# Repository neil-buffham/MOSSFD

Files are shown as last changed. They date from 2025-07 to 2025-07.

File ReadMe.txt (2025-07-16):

# Modular Open Source Split-Flap Display
(MOSSFD)
--------------------------------------------------------------------------------------------------------------------------------
This project is a Mechanical "Split-Flap" display based on:
- ESP32-WROOM-32D microcontroller
- 28BYJ-48 5V DC Stepper Motor
- ULN2003AN BWQ 2436C motor driver
- A3144 digital hall effect sensor

The display is designed to be built with identical modules based on these components. The modules can be connected in chain to form a display. For now, individual power is supplied to each unit, but on small scales, power can be daisy-chained instead. The modules I built use a JST 5 pin connector to connect RX, TX, "Detect", GND, and 5v, but you could use whatever 5 pin you felt like. (If you use VGA connectors please send me a picture). The hardware in the array is identical, but one module operates as the "Master", which is currently able to:
- Receive input from Serial Com (For example the Arduino IDE or other program)
- Scan this "Paragraph_message" for its own unique (mac-based) ID and perform the assigned command
- Forward this message to the other modules.

The other modules in the array scan the paragraph_message for their ID, and perform the command connected to their ID.

Current commands include (with a few notes about upcoming changes)
any letter    - Check if the character is in their index/drum, then move to that character.
***INFO       - Print current information                    //update
***ZERO       - Re-index using magnet			     //Possibly add slow zero
***<number>   - Move to flap index by number                 //Verify working after combined logic
***POS        - Print current step and degree position       //Possibly integrate to info / delete
***LIST       - Print character index list                   //.
***RESET      - Restart the ESP32                            //.
***REV        - Measure steps in one revolution              //Probably delete
***COUNT      - Show magnet pass count                       //Integrate/delete
***MOVE <N>   - Move forward by N steps                      //Delete
***ZOFFSET    - Set magnet-to-flap offset in degrees         //Cleanup + clean debug
***OFFSET     - Set global step offset                       //Cleanup + clean debug
***RESETCONFIG - Reset stored config to default values       //.
***HELP       - Show this help message                       //Update to match
***LEFTMODE   - Enable left-module input mode                //Update to match new logic
****[message] - Inject paragraph_message (for dev testing)   //Note: only available in MasterMode

At present the master module is kind of buggy, and needs some notable firmware work. It is not capable yet of creating the "paragraph_message", but will hopefully be able to do so soon. For now, I've been using a python script to parse text into a use-able paragraph message, which is then sent via Serial comm (Baud 11520 for PC -> Module communication) to the master module.

The paragraph_message is composed as follows:
**** //denotes that the following is a paragraph_message
[] //the beginning/end of the contents of the paragraph_message
{} //encompasses the master ID, which is sent at the beginning of each paragraph_message. This will be utilized later in development
| //divides the message from the master into chunks that are applicable to each unit
: //divides the portion of the message that is applicable to each unit into sections

Example: 9 module display, showing:
012345678

****[{14146C1C4278}|14146C1C4278:0:0|E0F76B1C4278:1:0|0445470B65F4:2:0|F893963B015C:3:0|2C1A6D1C4278:4:0|9CDC550B65F4:5:0|5CB469BF1388:6:0|1CF861BF1388:7:0|848A6C1C4278:8:0]

For the same command being sent to all modules, FFFF can be used. Ex:
- FFFF Character Commands //Set all modules to the same character, in this example a tilde.
 	****[{FFFF}|FFFF:~:0]
- FFFF Zero Commands //"Zero" all modules, re-indexing the start position using the hall effect sensor and the magnet
 	****[{FFFF}|FFFF:***ZERO:0]
- FFFF Reset Commands //Roughly equivalent to hitting the reset button. Makes the modules perform the startup sequence, which includes zero-ing.
 	****[{FFFF}|FFFF:***RESET:0]

//note: several of these functions are probably broken as of 7/15/2025
--------------------------------------------------------------------------------------------------------------------------------
I drew a custom PCB to be optionally used to house the Arduino and motor driver and provide more streamlined assembly (Just screw in your cables, assemble the 3d printed parts, and hot glue in the Hall effect, if you are into that kind of thing. It is NOT required, and I attempted to document the parts well in the spreadsheet. (There is a BOM as well.) If you choose to use the PCB, you will need to either solder jumper wires or get a bunch of jumping pins, as the "custom" non-esp32-standard-breakout parts are almost all in the bottom half and electrically isolated in case you change your mind and just want to use it as an ESP32 breakout. For reference, I was able to order 10 PCBA (assembled) units for $20 a pop (I don't like to think about it, questionably wise), and 20 non-assembled units for a "total" of $38.34 + $28 in import fees, which equates to ~$66.34 total or $3.34 per un-assembled part-less board. The Google sheets has a much better breakdown. Essentially, if you want to pay $15 per module for electronics and $5-$8 in printing costs, don't get a PCBa order. If you want to pay $40 for electronics and also $5-$8 for printing costs but reduce the assembly to screwing down 13 to 23 labeled cables (for left com, right com, Hall effect, and then possibly top / bottom comm {which are not supported in firmware yet}) and plugging in the motor cable, get the PCBA. If you want to pay about $18 per module for electronics and have a lot of soldering to do on top of the above cable-screwing, but prefer "solder in these headers" to "Attach D34 to the hall effect sensor OUT pin, which needs to have a 10k Resistor wired to the 3.3v pin...", then get a non-assembled PCB and order the parts. If you want to figure out import/duty fees, order the pcb components for assembly from China. Otherwise, Amazon has most of the parts, and if you find the right angle SMD xt30 you are a wizard.
--------------------------------------------------------------------------------------------------------------------------------
## License

This project uses a dual license approach:

- **Code (firmware, Arduino libraries)**: [GNU GPL v3.0](./LICENSE)
- **Design files (STLs, skp, skb, 3mf, fusion, onshape, other CAD, schematics, images, etc.)**: [Creative Commons BY-SA 4.0](./LICENSE.design)

Unless otherwise noted, source code files fall under GPLv3, and non-code files under CC BY-SA.
--------------------------------------------------------------------------------------------------------------------------------
### Disclaimer of Patent Liability

These files are provided under open licenses (GPL and CC BY-SA), but no patent rights are granted or implied.  
If use of this project or any of its parts infringes on third-party patents, you use it at your own risk.  
The author makes no warranties regarding patent freedom.
--------------------------------------------------------------------------------------------------------------------------------
### Disclaimer of Warranty

This project is provided "as is", without warranty of any kind — express or implied — including but not limited to the warranties of merchantability, fitness for a particular purpose, and noninfringement.  
In no event shall the author be liable for any claim, damages, or other liability arising from the use of this project, whether in an action of contract, tort, or otherwise.  
Use it at your own risk.
--------------------------------------------------------------------------------------------------------------------------------
In respect to the license, essentially you can:

- [✓] Use this project for personal or commercial purposes  
- [✓] Modify the code and designs  
- [✓] Share or remix your modified versions  
- [✓] Sell hardware or software based on it  

As long as you:

- [*] **Share improvements** under the same licenses (GPL for code, CC BY-SA for designs)  
- [*] **Give credit** to the original author (Neil Buffham)  
- [*] **Include the original license texts** when redistributing  
- [ ] **Do not** apply DRM or restrict others from doing these same things 

See the full license texts for legal details:  
- `LICENSE` for code (GPL v3)  
- `LICENSE.design` for designs (CC BY-SA 4.0)

Note: This is a human-friendly summary. The full license texts are authoritative and take precedence.
--------------------------------------------------------------------------------------------------------------------------------
Used in this project:

Overpass Mono Font  
- Source: https://fonts.google.com/specimen/Overpass+Mono  
- License: SIL Open Font License 1.1 (OFL) — https://openfontlicense.org  
- Copyright: © 2024 Red Hat, Inc.  
- Permission is granted to use, modify, and redistribute the font under the terms of the OFL.  
- The font is used in a slightly modified form for the characters on the flaps

AccelStepper Library  
- Source: https://docs.arduino.cc/libraries/accelstepper/  
- GitHub: https://github.com/waspinator/AccelStepper  
- License: GNU GPL v3.0 — https://www.gnu.org/licenses/gpl-3.0.html  
- Author: Mike McCauley / AirSpayce  
- The AccelStepper library is used in firmware to control the stepper motor.

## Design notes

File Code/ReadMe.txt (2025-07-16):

/*See Readme file. V005 attempts to overcome rounding float issues that
were resulting in the displayed index being off by 1 in V004.

V2005 includes:
- Better help menu
- (new) Info command
- added manually assigned steps for each flap in flap_index.h
- added a value and a function to apply adjustments to this value
- cleaned print functions to have divider lines between

Iterated to v2006 because it works now, and some features in v2006 may
interrupt active process' and change the logical flow of the offset-setting
commands. Thanks for reading.
*/

/*You will likely need to download a windows driver depending on your
ESP32 Board of choice. You will also need to add the ESP32 boards to
your arduinno IDE. Below is an example board and driver needed:

https://a.co/d/9pYIOlR
https://www.silabs.com/developer-tools/usb-to-uart-bridge-vcp-drivers?tab=downloads
for this board, the "Universal Windows Driver" works. Go to device manager and find
the device, then select the downloaded/extracted driver for "update driver" 

For me it showed up under the "Other Devices" as CP2102 USB to UART Bridge Controller
If you select the folder one level above x64 / x86 etc. it finds the correct driver.

In the Arduino IDE, I selected the ESP32 Dev Module as the board.
*/

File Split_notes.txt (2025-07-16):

Next firmware goals:
- Move back to a single-logical parsing situation by having a variable ActiveListenSerial, this way hopefully
   we can define multiple serial connections, but do our parsing based on what serial is listened to at present.
- With that, possibly combine back into one firmware instead of a forked Master/Slave pair
- Potentially provision for a button or switch or jumper to change between LEFTMODE and MASTERMODE
- Clean up the info and Zoffset data/debug information
- Add a motor power off timeout function
- Add a permanent variable that serves like an odometer, just because it would be interesting and we are already tracking rotations.
- Update available commands:

---
Available Commands:
***INFO       - Print current information                    //update
***ZERO       - Re-index using magnet			     //Possibly add slow zero
***<number>   - Move to flap index by number                 //Verify working after combined logic
***POS        - Print current step and degree position       //Possibly integrate to info / delete
***LIST       - Print character index list                   //.
***RESET      - Restart the ESP32                            //.
***REV        - Measure steps in one revolution              //Probably delete
***COUNT      - Show magnet pass count                       //Integrate/delete
***MOVE <N>   - Move forward by N steps                      //Delete
***ZOFFSET    - Set magnet-to-flap offset in degrees         //Cleanup + clean debug
***OFFSET     - Set global step offset                       //Cleanup + clean debug
***RESETCONFIG - Reset stored config to default values       //.
***HELP       - Show this help message                       //Update to match
***LEFTMODE   - Enable left-module input mode                //Update to match new logic
****[message] - Inject paragraph_message (for dev testing)   //Note: only available in MasterMode

Type any single character to move to that flap.              //Eh, probably fine

---

Current array:
14146C1C4278
E0F76B1C4278
0445470B65F4
F893963B015C
2C1A6D1C4278
9CDC550B65F4
5CB469BF1388
1CF861BF1388
848A6C1C4278

D4836C1C4278 //known issues

****[{14146C1C4278}|14146C1C4278:0:0|E0F76B1C4278:1:0|0445470B65F4:2:0|F893963B015C:3:0|2C1A6D1C4278:4:0|9CDC550B65F4:5:0|5CB469BF1388:6:0|1CF861BF1388:7:0|848A6C1C4278:8:0]

****[{14146C1C4278}|D4836C1C4278:***reset:0]

---
Current Firmwares: V2009-2_Master, V2009-3_Slave
Working:
- Space character
- FFFF Character Commands
 	****[{FFFF}|FFFF:~:0]
- FFFF Zero Commands
 	****[{FFFF}|FFFF:***ZERO:0]
- FFFF Reset Commands
 	****[{FFFF}|FFFF:***RESET:0]

NOT WORKING:
- the characters - on only the master firmware. Slave works fine.
 	Scratch that. It was finnicky but went eventually.
 	- / ,

- Master module individual commands finnicky
 	- Help works
 	- Reset and Zero do not
 	- Seems like the rest of the commands don't work (They are split into a separate portion in code)

***Zoffset0 - Displayed "," when commanded character "%"
***Zoffset72 - Displayed "@" when commanded character "%"
***Zoffset144 - Displayed '"' when commanded character "%"
***Zoffset216 - Displayed '!' when commanded character "%"
***Zoffset4032 - Displayed '/' when commanded character "%"
***Zoffset353 - Displayed '&' when commanded character "%"

***Zoffset90 - Displayed '@' when commanded character "%"

/*
  Zero Offset Reference Table (evenly spaced around 91.00°)

  Use with ***ZOFFSET<degrees> command
  Each row represents a full-degree step
  One flap ≈ 6.32°

// Steps   Degrees     Flap Offset (approx)
// ------  --------     ---------------------
//   927     81.47°         -1.50 flaps
//   939     82.50°         -1.35 flaps
//   951     83.53°         -1.20 flaps
//   963     84.56°         -1.04 flaps
//   975     85.59°         -0.90 flaps
//   987     86.62°         -0.75 flaps
//   999     87.66°         -0.60 flaps
//  1011     88.69°         -0.45 flaps
//  1023     89.72°         -0.30 flaps - two modules are currently set to this
//  1035     90.75°         baseline (ideal)
//  1047     91.78°         +0.15 flaps
//  1059     92.81°         +0.30 flaps
//  1071     93.84°         +0.45 flaps
//  1083     94.88°         +0.60 flaps
//  1095     95.91°         +0.75 flaps
//  1107     96.94°         +0.90 flaps
//  1119     97.97°         +1.04 flaps
//  1131     99.00°         +1.20 flaps
//  1143    100.03°         +1.35 flaps
//  1155    101.06°         +1.50 flaps

*/

---

2 - Motor_offset
3 - Bottom
3 - Drum_57
3 - Drum_57_lid
4 - Right_Wall
7 - Left_wall
7 - Lid_(wide)
8 - Motor_Bracket
2 - PCB_tray
2-5 - Flaps (Special Characters)

Microcontroller:
ESP32-WROOM-32D

28BYJ-48 5V DC Stepper Motor with
ULN2003AN BWQ 2436C motor driver chip in a breakout board

A3144 hall effect sensor (3 pin) - note that the side with the writing is the front face, and needs to interact with a magnet's South pole.
  Pin 1 (left)   -   VCC (typically 5V)
  Pin 2 (middle) -   GND
  Pin 3 (right)  -   OUT (signal to ESP32, use 10kohm pullup resistor wired to 3.3v)
    one wire straight from the pin to the esp32
    one wire from the esp32 through the 10kohm resistor to the 3.3v pin.

Connectors for module to module communication:
  1 - VCC (Shared 5v Power)
  2 - GND (Shared ground)
  3 - RX (incoming data)
  4 - TX (outgoing data)
  5 - Presence/detect (sense neighboring modules/ESP's) //likely not used in current-version code

Buttons:  //these are not populated in current version hardware.
  BTN1 - GPIO36 (VP) - Use internal Pullup resistor and wire opposite to GND
  BTN2 - GPIO39 (VN) - Use internal Pullup resistor and wire opposite to GND

Wiring notes:
5V and GND bus bars:
10 screw bus bar for Ground
  4 for the top/bottom/side/side communication
  2 for the buttons
  1 for the type c 5VIN ground connector
  1 for the ESP32 ground connector
  1 for the Hall Effect Sensor
  1 for the Motor Driver

8 screw bus bar for 5V
  4 for the top/bottom/side/side communication
  1 for the type c 5VIN connector
  1 for the ESP32 VIN
  1 for the Hall Effect Sensor
  1 for the Motor Driver

---
Goal for now: Get a "Send-only" network together where there are only two code types: The Master unit, and Slave units.
The master parses a "serial monitor" input from the Arduino IDE, and spits out a paragraph style text over a module-to-module
serial connection (RX and TX). Each slave unit knows its own identifier, but nothing else in relation to the display. They
don't "dabble" in anything besides searching the serial-received message for the chunk that contains their identifier, forwarding
the serial message on to the right, and following the command that they received. The only other thing that each module needs to
"be aware" of is FFFF. They should be set up to look for FFFF in the paragraph message that is sent in the same way they look for
their own ID, and follow commands stated to FFFF. There might need to be own ID vs FFFF logic later, but not yet.

While perhaps not the most logical, for now I want each module, including the master, to both store and process the paragraph
message. This will hopefully avoid too many branches of active code that need to function together (ex. master code execution vs.
slave code execution + timing + "finished" handling, etc.

I think a logical way to do this will be to have Some pre-determined dividers:
[] //means the beginning/end of the message that is sent from the master
{} //encompass the master ID
| //divide the message from the master into chunks that are applicable to each unit
: divide the portion of the message that is applicable to each unit into sections

The sections:
[{MasterID}|SlaveID:Character or code:Status|SlaveID:Character or code:Status

Third value: status
0 = no modifier //go to character or perform code immediately. Eventually blank might call this function as well.
1 = no command detected yet
7 = parse_error //could not parse a useable command out of the paragraph_message
8 = execution_error //the command was not completed
9 = complete //the last command was completed correctly - used for internal recording, not communication yet.

/*
//- Soon we may try to implement "hold"/wait functionality, but not yet.
 = Hold //Store value but don't go yet
 =  Go //Go to stored value, or "" if no value present //There should always be a value present
*/

/*
//- The following are in ideation only and should be nearly entirely ignored. Do not cater to them.
 = Finished //From the master module's perspective, this is not a "TX" value, this would be recieved.
 = Received //Character received
*/

Example setup:
Master: 14146C1C4278
Slave1: 0445470B65F4
Slave2: 848A6C1C4278

Example outputs:
ABC
No delays or holds, just go now:
[{14146C1C4278}|14146C1C4278:A:0|0445470B65F4:B:0|848A6C1C4278:C:0]

DOG
No delays or holds, just go now:
[{14146C1C4278}|14146C1C4278:A:0|0445470B65F4:B:0|848A6C1C4278:C:0]

Reset all modules now:
[{14146C1C4278}|FFFF:***Reset:0]

Zero all modules now:
****[{FFFF}|FFFF:***ZERO:0]

---

With this in mind, I think that each module will need local processing for the following:
- Serial receive(Left)
- Serial write(Right)

- A variable for it's own ID (already implemented)
- A "Status" variable that notes if the module is ready to receive the p. message
- long text variable to store the paragraph

current_command - A variable to store the command or character decided by the paragraph message
current_command_status - A variable to store the status declared by the paragraph message

- Several Boolean variables:
  - One to record that a new paragraph message has been received
  - Another to record that the current paragraph message has been forwarded to the right TX
  - Another to mark if the current message has been processed
//This should conclude what is needed to interact with the paragraph message.
//note that there likely are some ?empirical? errors with this logic's ability to display
//characters such as " : | { } [ ]  .I recognize this, but if we can get anything working
//then we will try to fix that later. We will not be modifying the flap_index.h file to
//accommodate this code structure at all, and just hoping for the best until it breaks.

Example slave logical flow:
ready_for_paragraph_message = FALSE
//insert standard startup procedure here
current_command - Either NULL or whatever is safe/easy to do as an alternative
current_command_status -
ready_for_paragraph_message = TRUE
//print "Ready to receive paragraph message.
paragraph_message = NULL
paragraph_message_received = FALSE
paragraph_message_sent = FALSE
paragraph_message_processed = FALSE

Left RX receives the following:
[{14146C1C4278}|14146C1C4278:A:0|0445470B65F4:B:0|848A6C1C4278:C:0]
//The logical flow of paragraph receiving/processing has not been covered yet, but know
//that the module sees the character ] and recognizes the message is complete.
paragraph_message_received = TRUE
ready_for_paragraph_message = FALSE
paragraph_message = "[{14146C1C4278}|14146C1C4278:A:0|0445470B65F4:B:0|848A6C1C4278:C:0]"

Right TX sends the following:
[{14146C1C4278}|14146C1C4278:A:0|0445470B65F4:B:0|848A6C1C4278:C:0]
paragraph_message_sent = TRUE

if paragraph_message == not NULL:
  if paragraph_message_sent == TRUE:
    if paragraph_message_processed = FALSE:
/*
Look for the following:
[ - denotes a paragraph_message that is useable
then run one scan through, looking for "FFFF"
If the character ] is found and no FFFF is found, there isn't an FFFF command
If it is found, then DO NOT run the second processing of the paragraph_message.
if it isn't found, we need to search the paragraph_message again to find this unit's character ID.
IF you find this unit's character ID, do the following (relative to the just-detected character ID):
Immediately following the character ID there should be a ":" character.
Detect the section of text between this instance of ":" and the next instance of the character ":"
Record this value as the "current_command".
The current_command was defined by a closing ":" character. Store any characters
that follow this as the current_command_status, until you reach either ":" or "|".

Once these values have been populated, stop processing the paragraph_message. There
is no need to look through the rest of it.

if the character "]" is detected and this module's ID has not been detected:
current_command = whatever a safe null value is
current_command_status = 7 // parse_error

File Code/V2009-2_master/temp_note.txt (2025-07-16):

Here is the current code. Note that it is just V2008 renamed to V2009_slave at present. Also note that very minor changes have been made to the text you returned, which is stored as V2009_slave_goals.txt (thanks, it was very helpful). Based on all of this information, can you generate code that performs the functions discussed the previously discussed Serial monitoring/paragraph_message - injection difference?

Please take the precautions necessary to keep whichever serial(s) are currently functioning ... functioning. For now, I want to add a function that puts the device in module-listening mode. This will mean a modification to the SplitFlapMotor.cpp file, so that we can have a *** function to make serialRead be accepting from the module to the left instead of the Arduino IDE. This needs to be off by default, and reset to off when the reset button is pushed. This way I can set the function on 2/3 modules in my test grid and keep the first module as a ~sudo master, but only different in that I can still write to him from the Arduino IDE.

Pardon me, I've had that drafted for a bit and didn't edit it. Before you generate anything, is this logically sound?

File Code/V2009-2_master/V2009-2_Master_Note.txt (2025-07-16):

There are a handful of issues with this "firmware", the two biggest ones being:
- You have to send the initial message several times before it will take. Once you've been sending messages (over Arduino IDE serial) for a bit it calms down. It is probably due to how the Serial input is read/parsed (rather than the message itself being parsed once it is received).
- Many of the commands are not available for use over Arduino IDE Serial Monitor Input. They may or may not work if you send the command to the master module through a "Paragraph_Message". No promises.

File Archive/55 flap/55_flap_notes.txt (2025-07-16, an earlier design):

I was pretty happy with the 55 flap drum size, but I didn't want to have gears between the motor drive shaft and the drum, because it would be one more point of friction/failure/variable. The motor would probably have fit in this drum, but not without a gear to handle the offset, or some other BS-ery.

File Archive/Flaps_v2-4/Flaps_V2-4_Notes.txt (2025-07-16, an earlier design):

The Flaps V2-4 were fine, but there weren't unified build plate layouts, and the vertical gap between the flaps was larger than I had hoped for.

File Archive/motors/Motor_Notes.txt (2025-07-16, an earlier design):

Sketchup file of the motor used in the project, to aid in drawing. I won't pretend the drawing is a great fit, but it's something, and the friction and lack of motor retention system within the corresponding bracket were *Totally strategic, well planned design choices, rather than a ...

... huh, guess this hasn't stopped working yet ...

moment.

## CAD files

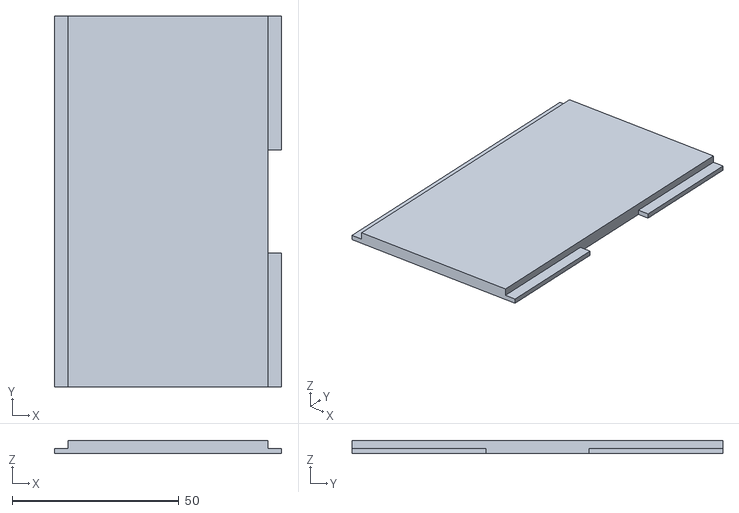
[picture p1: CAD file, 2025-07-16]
3d_Sketchup_Current/Back_bracket/Back_Bracket_1.stl
68.0 x 111.0 x 4.00

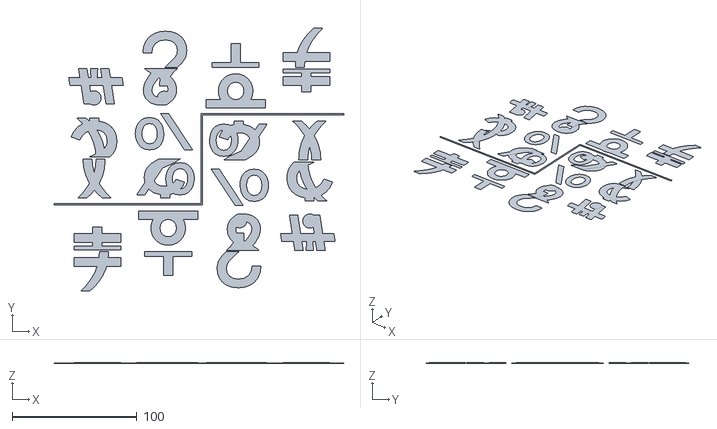
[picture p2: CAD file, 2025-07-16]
3d_Sketchup_Current/Flaps_V2-5/Flaps2005_Special2_Letter.stl
232.6 x 210.7 x 1.00

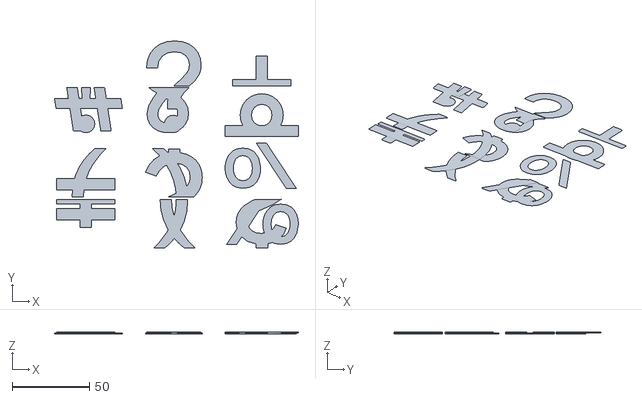
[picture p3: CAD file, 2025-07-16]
3d_Sketchup_Current/Flaps_V2-5/K1_plate_arranged/Flaps_v2005_Special_Letter_K1.stl
157.7 x 133.9 x 1.00

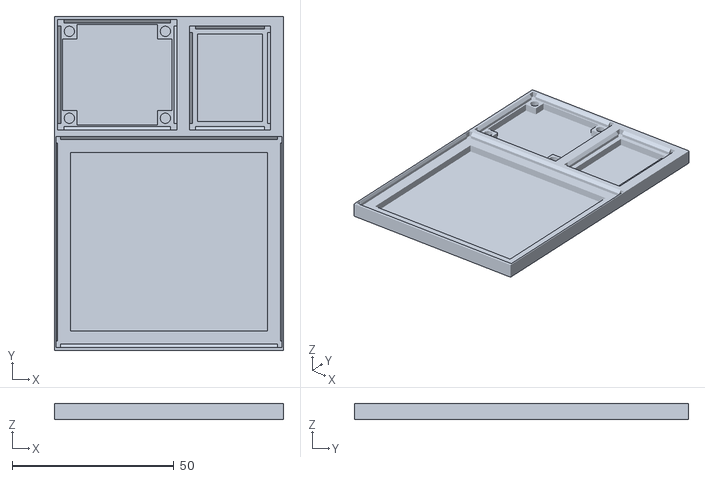
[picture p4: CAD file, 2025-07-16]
3d_Sketchup_Current/pcbtray/B1TrayV1.stl
70.8 x 103.4 x 5.00

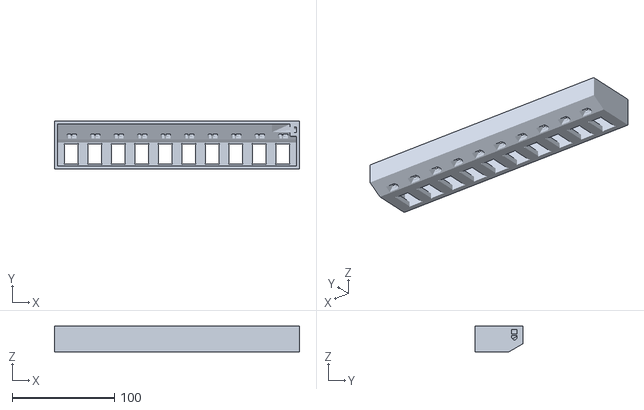
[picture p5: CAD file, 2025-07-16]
3d_Sketchup_Current/Switchboard/Switchboard_V1.stl
240.0 x 46.9 x 25.0

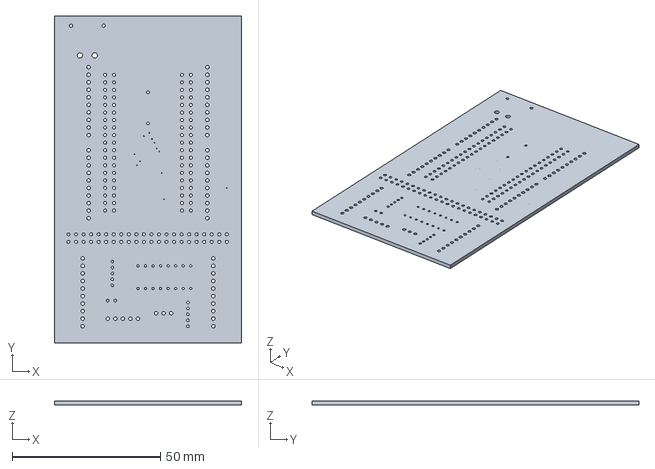
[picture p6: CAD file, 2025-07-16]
Custom_PCB/breakoutboard.step
63.0 x 110.0 x 1.41 mm

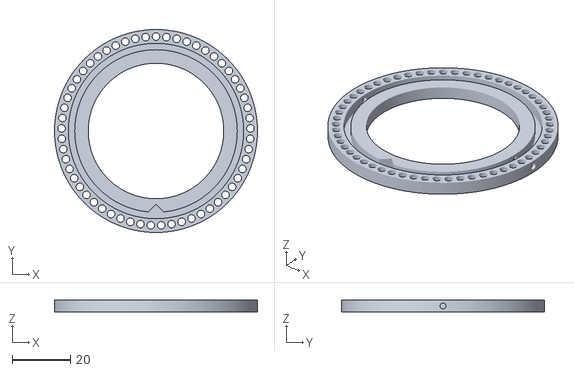
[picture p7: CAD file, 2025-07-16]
SFv2_Files/Drum_Lid_Motor_003.stl
69.7 x 69.7 x 4.00

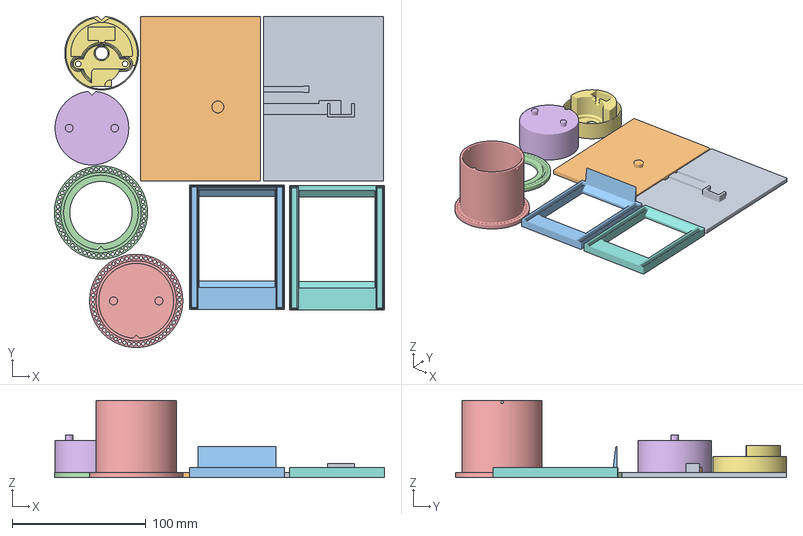
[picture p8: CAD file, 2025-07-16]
SFv2_Files/Prob_not_latest/Kobra_Slices/S1_Enclosure_V2004.3mf
247.0 x 247.5 x 57.9 mm
SF2_Right_Wall003.stl
SF2_LeftWall002.stl
SF2_Lid_top_002.stl
SF2_Drum_Lid_Motor_003.stl
SF2_Drum_motorV2003.stl
SF2_Motor_offset002.stl
SF2_Motor_bracket008.stl
SF2_Bottom001.stl

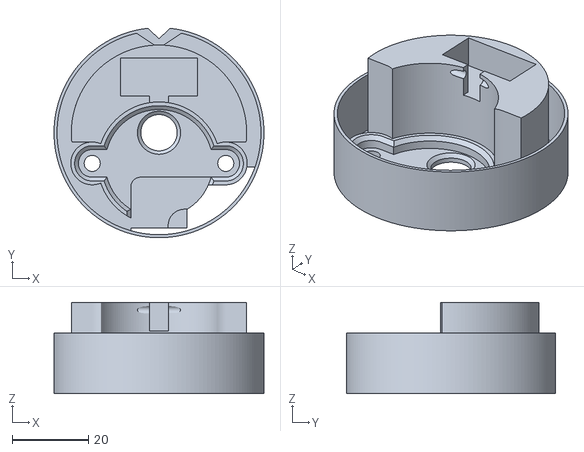
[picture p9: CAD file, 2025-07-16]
SFv2_Files/Prob_not_latest/SF2_Motor_bracket008.stl
55.1 x 54.9 x 24.0

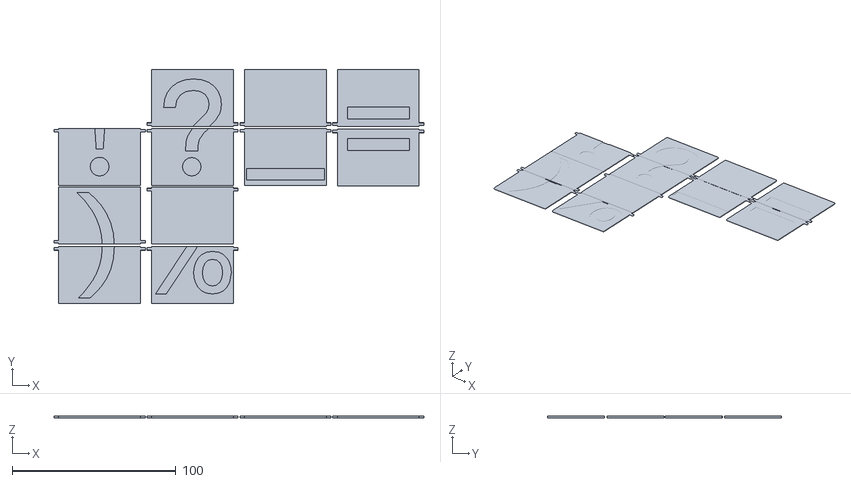
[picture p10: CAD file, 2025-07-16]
3d_Sketchup_Current/Flaps_V2-5/Flaps2005_Special_Flap.stl
226.2 x 143.1 x 1.00

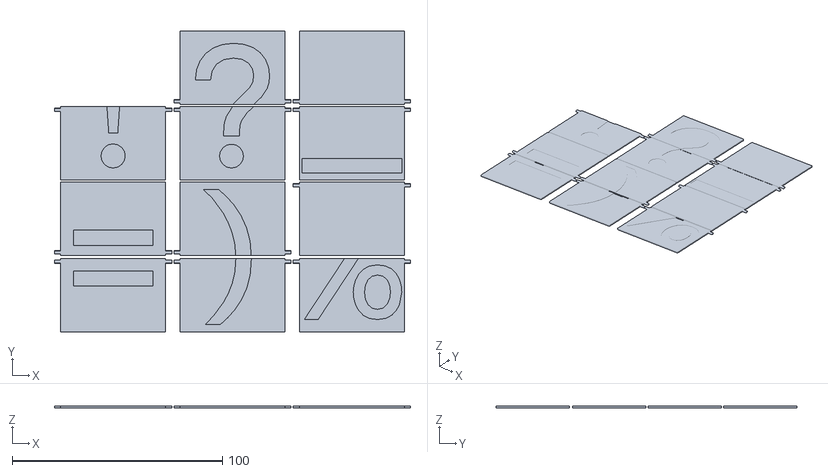
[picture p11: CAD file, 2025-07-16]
3d_Sketchup_Current/Flaps_V2-5/K1_plate_arranged/Flaps_v2005_Special_Flap_K1.stl
169.4 x 143.1 x 1.00

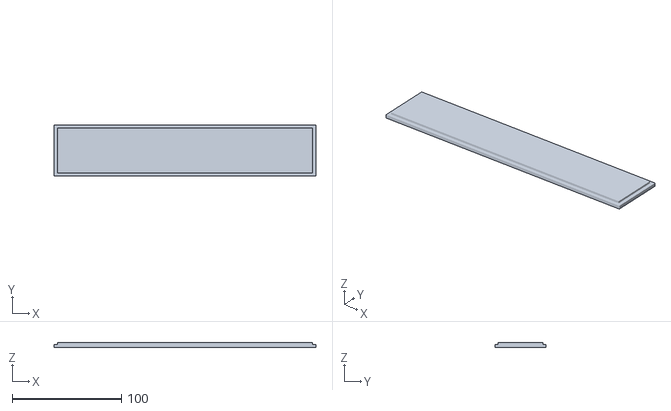
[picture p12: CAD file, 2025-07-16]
3d_Sketchup_Current/Switchboard/bottom_1.stl
239.7 x 47.0 x 4.90

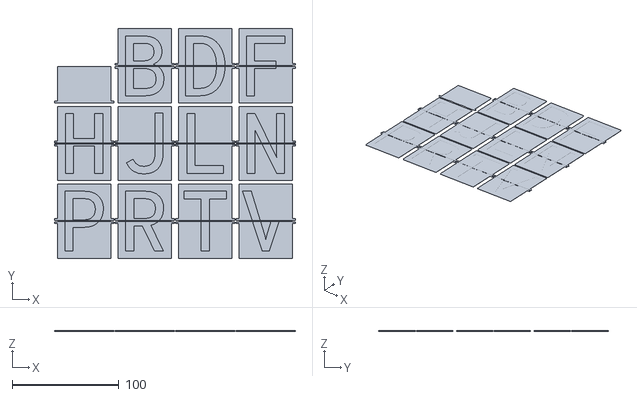
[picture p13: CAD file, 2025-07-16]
SFv2_Files/Prob_not_latest/Flaps_2-2_A-U_flap.stl
226.2 x 215.6 x 1.00

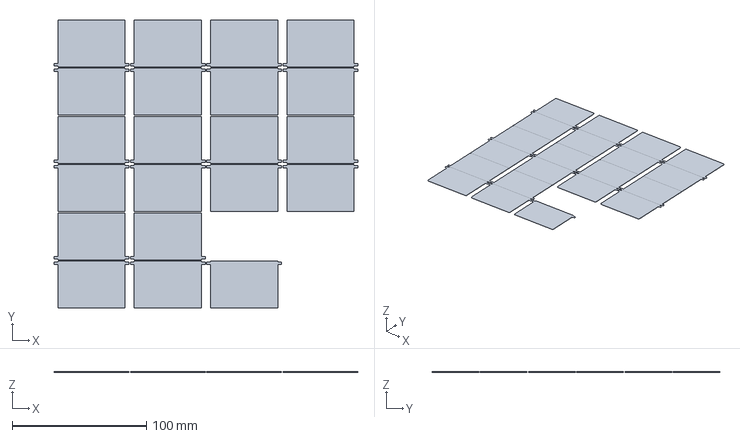
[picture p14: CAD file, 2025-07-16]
SFv2_Files/Prob_not_latest/Kobra_Slices/K3_Extra_Flaps.3mf
226.2 x 214.6 x 1.00 mm

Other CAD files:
SFv2_Files/Back_Bracket_1.stl
3d_Sketchup_Current/Flaps_V2-5/Flaps2005_Special_Letter.stl
3d_Sketchup_Current/pcbtray/ETrayV3.stl
SFv2_Files/Lid_007_wide.stl
3d_Sketchup_Current/Back_bracket/Back_Bracket.skp
3d_Sketchup_Current/Flaps_V2-5/Flaps2005_A_W-Flap.stl
3d_Sketchup_Current/Flaps_V2-5/Flaps2005_A_W-Letter.stl
3d_Sketchup_Current/Flaps_V2-5/Flaps2005_Special2_Flap.stl
3d_Sketchup_Current/Flaps_V2-5/Flaps2005_X-Spec_Flap.stl
3d_Sketchup_Current/Flaps_V2-5/Flaps2005_X-Spec_Letter.stl
3d_Sketchup_Current/Switchboard/Switchboard_Arrange.skp
3d_Sketchup_Current/Switchboard/Switchboard_Export.skp
3d_Sketchup_Current/Switchboard/Switchboard_elements.skp
3d_Sketchup_Current/Switchboard/bottom_1.skp
3d_Sketchup_Current/pcbtray/ETrayV2.skp
3d_Sketchup_Current/pcbtray/ETrayV2.stl
Archive/50 flap/50flap_export.skp
Archive/50 flap/50flap_v2.stl
Archive/50 flap/50flapshaft.stl
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

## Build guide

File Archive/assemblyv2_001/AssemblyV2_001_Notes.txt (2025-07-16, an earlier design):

This was created in Sketchup, and is one of the earliest renditions of the project. It worked okay, but was pretty rudimentary. I didn't have a multicolor 3d printer and didn't want to make 3mfs. (I still don't want to, but what else is new). So I just printed off sheets of paper and glued them on. Time consuming, and questionably permanent.

Sketchup (make 2017) has to have a handful of extensions to make 3d printing models "well", and I won't pretend it's a great solution, but monthly subscriptions for things that don't require continuous upkeep (for example a mail/SMTP server, or other legitimate hosting service) are pretty not cool. Also, a lot of CAD "licenses" have weird stipulations like you don't actually own the design, or you can only make x amount of money off of something drawn in said program. 
So, no real circles, but you own your not-real circles.

I switched to using onshape, despite having just recently re-learned Fusion360. Eventually I hope to have parallel files in several types, based off of "Master" dimension/cad/blueprint files, but time will tell. I figured the onshape trade-off of no privacy for your files, but no financial cap (Which I probably misunderstood, but such is non-lawyer life) might be more friendly for file sharing / "Ownership".

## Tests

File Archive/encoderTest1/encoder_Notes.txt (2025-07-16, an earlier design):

Yeah, nah. The mouse wheel encoders I was using were not precise enough, and other options are either too expensive and/or large if they have the needed precision. Modified the Left wall to fit the encoder and ran a bunch of tests. I couldn't get decent working code to get use-able resolution out of the encoder because 57 flaps means 360 degrees / 57 is ~6ish degrees, which would be barely use-able results.

We will just have to shoot for avoiding step skips.

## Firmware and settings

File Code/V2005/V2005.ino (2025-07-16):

/*See Readme file. V005 attempts to overcome roudning flaot issues that
were resulting in the displayed index being off by 1 in V004.

V2005 includes:
- Better help menu
- (new) Info command
- added manually assigned steps for each flap in flap_index.h
- added a value and a function to apply adjustments to this value
- cleaned print functions to have divider lines between

Iterated to v2006 because it works now, and some features in v2006 may
interrupt active process' and change the logical flow of the offset-setting
commands. Thanks for reading.
*/


#include <AccelStepper.h>
#include "flap_index.h"  // Include the flap character index

// --- Pin assignments ---
const int IN1 = 5;    // Stepper coil A1
const int IN2 = 4;    // Stepper coil A2
const int IN3 = 2;    // Stepper coil B1
const int IN4 = 15;   // Stepper coil B2
const int HALL_SENSOR_PIN = 34;  // Hall Effect sensor OUT

const int STEPS_PER_REV = 4096;  // 28BYJ-48 in half-step mode
const float STEPS_PER_DEGREE = STEPS_PER_REV / 360.0;
long zeroOffsetDegrees = 91;  // Offset from magnet detection position (was OFFSET_DEGREES)
long stepOffset = 0;  // Offset applied to all flap steps


AccelStepper stepper(AccelStepper::HALF4WIRE, IN1, IN3, IN2, IN4);
bool motorBusy = false;
int magnetPassCount = 0;

void indexToMagnet() {
  Serial.println("Searching for magnet to zero position...");
  stepper.setMaxSpeed(1000);  // Fast speed for zeroing
  stepper.setAcceleration(500);

  // Advance by 1/8 of a rotation before checking for the magnet
  long preOffsetSteps = STEPS_PER_REV / 8;
  stepper.moveTo(preOffsetSteps);
  while (stepper.distanceToGo() > 0) {
    stepper.run();
  }

  stepper.moveTo(stepper.currentPosition() + 100000); // Large move target after offset
  while (digitalRead(HALL_SENSOR_PIN) != LOW && stepper.currentPosition() < 100000 + preOffsetSteps) {
    stepper.run();
  }


  // Move forward by the offset degrees to avoid backward motion
  long offsetSteps = zeroOffsetDegrees * STEPS_PER_DEGREE;

  stepper.moveTo(stepper.currentPosition() + offsetSteps);
  while (stepper.distanceToGo() > 0) {
    stepper.run();
  }

  // Reset position to 0 after offset
  stepper.setCurrentPosition(0);
  magnetPassCount = 0;  // Reset magnet pass counter
  Serial.println("Magnet detected and offset applied. Position zeroed.");
  delay(500);
}

void detectStepsPerRevolution() {
  Serial.println("Measuring full revolution steps...");
  indexToMagnet();

  stepper.setMaxSpeed(200);  // Controlled slow speed
  stepper.setAcceleration(100);

  long startPos = stepper.currentPosition();
  stepper.moveTo(startPos + 100000);  // Arbitrary large move

  bool magnetPassedOnce = false;
  bool waitingForSecond = false;
  long magnetFirstStep = 0;
  long stepsBetween = 0;
  unsigned long magnetCooldown = 0;

  while (stepper.distanceToGo() > 0) {
    stepper.run();

    if (digitalRead(HALL_SENSOR_PIN) == LOW) {
      if (!magnetPassedOnce) {
        magnetFirstStep = stepper.currentPosition();
        magnetPassedOnce = true;
        waitingForSecond = true;
        magnetCooldown = millis();
        Serial.println("First magnet detection recorded.");
      } else if (waitingForSecond && millis() - magnetCooldown > 800) {
        stepsBetween = stepper.currentPosition() - magnetFirstStep;
        Serial.print("Steps between magnet detection / Steps per Revolution: ");
        Serial.println(stepsBetween);
        break;
      }
    }
  }
}

void setZeroOffsetDegrees(long offset) {
  Serial.println("-------------------------------------------");
  Serial.print("Previous Zero Offset (degrees): ");
  Serial.println(zeroOffsetDegrees);

  zeroOffsetDegrees = offset;

  Serial.print("New Zero Offset (degrees): ");
  Serial.println(zeroOffsetDegrees);
}


void setStepOffset(long offset) {
  Serial.println("-------------------------------------------");
  Serial.print("Previous Offset: ");
  Serial.println(stepOffset);

  stepOffset = offset;

  Serial.print("New Offset: ");
  Serial.println(stepOffset);
}


void moveSteps(int steps) {
  Serial.print("Moving forward ");
  Serial.print(steps);
  Serial.println(" steps...");
  motorBusy = true;
  stepper.moveTo(stepper.currentPosition() + steps);
  while (stepper.distanceToGo() != 0) {
    stepper.run();
  }
  Serial.println("Done.");
  motorBusy = false;
}

void goToCharacter(char inputChar) {
  inputChar = toupper(inputChar);
  int targetIndex = -1;
  for (int i = 0; i < NUM_FLAPS; i++) {
    if (flapCharacters[i] == inputChar) {
      targetIndex = i;
      break;
    }
  }

  if (targetIndex == -1) {
    Serial.println("Character not in index.");
    return;
  }
  goToIndex(targetIndex);
}

void goToIndex(int targetIndex) {
  long targetSteps = flapSteps[targetIndex] + stepOffset;  // Use precomputed step position

  long currentPosition = stepper.currentPosition();
  long currentStepMod = currentPosition % STEPS_PER_REV;
  if (currentStepMod < 0) currentStepMod += STEPS_PER_REV;  // Normalize to 0–4095

  long relativeTarget = targetSteps;
  if (targetSteps <= currentStepMod) {
    relativeTarget += STEPS_PER_REV;  // Always move forward
  }

  long absoluteTarget = currentPosition + (relativeTarget - currentStepMod);

  //Print expected character information
  Serial.print("Moving to index ");
  Serial.print(targetIndex);
  Serial.print(" (Character: '");
  Serial.print(flapCharacters[targetIndex]);
  Serial.println("')...");
  motorBusy = true;
  stepper.moveTo(absoluteTarget);
  while (stepper.distanceToGo() != 0) {
    stepper.run();
    if (digitalRead(HALL_SENSOR_PIN) == LOW) {
      static unsigned long lastMagnetTime = 0;
      if (millis() - lastMagnetTime > 500) {
        magnetPassCount++;
        lastMagnetTime = millis();
      }
    }
  }
  Serial.println("Done.");
  motorBusy = false;
}


void printPosition() {
  Serial.println("-------------------------------------------");
  Serial.print("Current Step Position: ");
  Serial.print(stepper.currentPosition());
  Serial.print(" | Degrees: ");
  Serial.println(stepper.currentPosition() / STEPS_PER_DEGREE);
}

void printIndexList() {
  Serial.println("-------------------------------------------");
  Serial.println("Character Index List:");
  for (int i = 0; i < NUM_FLAPS; i++) {
    Serial.print(i);
    Serial.print(": ");
    Serial.println(flapCharacters[i]);
  }
}

void printHelp() {
  Serial.println("-------------------------------------------");
  Serial.println("Available Commands:");
  Serial.println("***Info      - Print current information");
  Serial.println("***ZERO      - Re-index using magnet");
  Serial.println("***<number>  - Move to flap index by number");
  Serial.println("***POS       - Print current position in steps and degrees");
  Serial.println("***LIST      - Print character index list");
  Serial.println("***RESET     - Set current step position to 0");
  Serial.println("***REV       - Measure steps between magnet detections (1 revolution)");
  Serial.println("***COUNT     - Show number of magnet passes since last zero");
  Serial.println("***MOVE      - Move forward by a number of steps (e.g., ***MOVE 80)");
  Serial.println("***ZOFFSET    - Set offset (in degrees) from magnet during zeroing (e.g., ***ZOFFSET 91)");
  Serial.println("***OFFSET    - Apply global step offset to all flap indexes (e.g., ***OFFSET 12)");
  Serial.println("***HELP      - Show this help message");
  Serial.println();
  Serial.println("Type any single character to move to that flap.");
}


void printMagnetPassCount() {
  Serial.println("-------------------------------------------");
  Serial.print("Magnet has passed ");
  Serial.print(magnetPassCount);
  Serial.println(" times since last zeroing.");
}


void printInfo() {
  Serial.println("-------------------------------------------");
  Serial.print("Current Step Position: ");
  Serial.print(stepper.currentPosition());
  Serial.print(" | Degrees: ");
  Serial.println(stepper.currentPosition() / STEPS_PER_DEGREE);
  Serial.print("Magnet has passed ");
  Serial.print(magnetPassCount);
  Serial.println(" times since Zeroing");
  Serial.print("Zero Offset (Degrees): ");
  Serial.println(zeroOffsetDegrees);
  Serial.print("Step Offset (Steps): ");
  Serial.println(stepOffset);
}


void setup() {
  pinMode(HALL_SENSOR_PIN, INPUT);
  Serial.begin(115200);
  Serial.println("Starting Stepper Degree Test...");

  indexToMagnet();
}

void loop() {
  if (!motorBusy && Serial.available() > 0) {
    String input = Serial.readStringUntil('\n');
    input.replace('\r', ' ');  // Remove carriage return, preserve spaces

    input.trim();
    if (input.startsWith("***")) {
      String command = input.substring(3);
      command.toUpperCase();
      
      if (command == "ZERO") {
        indexToMagnet();
      } else if (command == "POS") {
        printPosition();
      } else if (command == "LIST") {
        printIndexList();
      } else if (command == "RESET") {
        stepper.setCurrentPosition(0);
        Serial.println("Stepper position reset to 0.");
      } else if (command == "REV") {
        detectStepsPerRevolution();
      } else if (command == "COUNT") {
        printMagnetPassCount();
      } else if (command.startsWith("MOVE")) {
        int moveStepsVal = command.substring(5).toInt();
        if (moveStepsVal > 0) {
          moveSteps(moveStepsVal);
        } else {
          Serial.println("Invalid step count for MOVE command.");
        }
      } else if (command.startsWith("OFFSET")) {
        long newOffset = command.substring(6).toInt();
        setStepOffset(newOffset);
      } else if (command == "HELP") {
        printHelp();
      } else if (command.startsWith("ZOFFSET")) {
        long newZOffset = command.substring(7).toInt();
        setZeroOffsetDegrees(newZOffset);
      } else if (command == "INFO") {
          printInfo();
      } else {
        int index = command.toInt();
        if (index >= 0 && index < NUM_FLAPS) {
          goToIndex(index);
        } else {
          Serial.println("Invalid command or index.");
        }
      }
    } else if (input.length() > 0) {
      char selectedChar = input.charAt(0);
      Serial.print("Character received: [");
      Serial.print(selectedChar);
      Serial.println("]");
      goToCharacter(selectedChar);
    }
  }
}

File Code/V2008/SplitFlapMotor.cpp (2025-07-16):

#include "SplitFlapMotor.h"
#include "flap_index.h"
#include "SFConfig.h"
SFConfig config;

SplitFlapMotor::SplitFlapMotor(int in1, int in2, int in3, int in4, int hallPin)
  : stepper(AccelStepper::HALF4WIRE, in1, in3, in2, in4),
    hallSensorPin(hallPin),
    zeroOffsetDegrees(91),
    stepOffset(0),
    magnetPassCount(0),
    motorBusy(false) {}

void SplitFlapMotor::begin() {
    pinMode(hallSensorPin, INPUT);
    stepper.setMaxSpeed(800);
    stepper.setAcceleration(400);

    config.begin();
    zeroOffsetDegrees = config.getZeroOffset();
    stepOffset = config.getStepOffset();
}

String SplitFlapMotor::getModuleID() {
  uint64_t chipid = ESP.getEfuseMac();
  char id[13];
  sprintf(id, "%02X%02X%02X%02X%02X%02X",
          (uint8_t)(chipid >> 40), (uint8_t)(chipid >> 32), (uint8_t)(chipid >> 24),
          (uint8_t)(chipid >> 16), (uint8_t)(chipid >> 8), (uint8_t)chipid);
  return String(id);
}

void SplitFlapMotor::indexToMagnet() {
  Serial.println("Searching for magnet to zero position...");

  bool magnetSeen = false;
  long startPos = stepper.currentPosition();
  long maxSteps = 4096 + (4096 / 8);
  stepper.moveTo(startPos + maxSteps);

  while (stepper.distanceToGo() > 0) {
    stepper.run();
    if (digitalRead(hallSensorPin) == LOW) {
      if (!magnetSeen) {
        magnetSeen = true;
        delay(5);
      } else {
        stepper.stop();
        break;
      }
    } else {
      magnetSeen = false;
    }
  }

  long offsetSteps = zeroOffsetDegrees * (4096.0 / 360.0);
  stepper.moveTo(stepper.currentPosition() + offsetSteps);
  while (stepper.distanceToGo() > 0) stepper.run();

  stepper.setCurrentPosition(0);
  magnetPassCount = 0;
  Serial.println("Magnet detected and offset applied. Position zeroed.");
  delay(500);
}

void SplitFlapMotor::detectStepsPerRevolution() {
  Serial.println("Measuring full revolution steps...");
  indexToMagnet();
  stepper.setMaxSpeed(200);
  stepper.setAcceleration(100);
  stepper.moveTo(stepper.currentPosition() + 100000);

  bool magnetPassedOnce = false;
  long magnetFirstStep = 0;
  long stepsBetween = 0;
  unsigned long magnetCooldown = 0;

  while (stepper.distanceToGo() > 0) {
    stepper.run();
    if (digitalRead(hallSensorPin) == LOW) {
      if (!magnetPassedOnce) {
        magnetFirstStep = stepper.currentPosition();
        magnetPassedOnce = true;
        magnetCooldown = millis();
        Serial.println("First magnet detection recorded.");
      } else if (millis() - magnetCooldown > 800) {
        stepsBetween = stepper.currentPosition() - magnetFirstStep;
        Serial.print("Steps per Revolution: ");
        Serial.println(stepsBetween);
        break;
      }
    }
  }
}

void SplitFlapMotor::resetConfig() {
  Serial.println("-------------------------------------------");
  Serial.println("Resetting configuration to defaults...");

  config.setZeroOffset(91);  // Default zero offset
  config.setStepOffset(0);   // Optional: you can omit this if you prefer

  zeroOffsetDegrees = 91;
  stepOffset = 0;

  Serial.println("Config reset complete.");
}


void SplitFlapMotor::setZeroOffsetDegrees(long offset) {
    Serial.println("-------------------------------------------");
    Serial.print("Previous Zero Offset (degrees): ");
    Serial.println(zeroOffsetDegrees);
    zeroOffsetDegrees = offset;
    config.setZeroOffset(offset);  // <-- Store persistently
    Serial.print("New Zero Offset (degrees): ");
    Serial.println(zeroOffsetDegrees);
}

void SplitFlapMotor::setStepOffset(long offset) {
    Serial.println("-------------------------------------------");
    Serial.print("Previous Offset: ");
    Serial.println(stepOffset);
    stepOffset = offset;
    config.setStepOffset(offset);  // <-- Store persistently
    Serial.print("New Offset: ");
    Serial.println(stepOffset);
}


void SplitFlapMotor::setZeroOffsetDegreesInteractive() {
  if (motorBusy) {
    Serial.println("Cannot change zero offset while motor is moving.");
    return;
  }

  Serial.println("-------------------------------------------");
  Serial.print("Current Zero Offset (degrees): ");
  Serial.println(zeroOffsetDegrees);
  Serial.println("Change zero offset? (y/n):");

  while (Serial.available() == 0);
  char response = Serial.read();
  while (Serial.available()) Serial.read();  // Clear buffer

  if (response == 'y' || response == 'Y') {
    Serial.println("Enter new zero offset (in degrees, integer):");
    while (Serial.available() == 0);
    String line = Serial.readStringUntil('\n');
    line.trim();
    zeroOffsetDegrees = line.toInt();
    config.setZeroOffset(zeroOffsetDegrees);  // <-- Save persistently
    Serial.print("New Zero Offset (degrees) set to: ");
    Serial.println(zeroOffsetDegrees);
  } else {
    Serial.println("No changes made.");
  }
}


void SplitFlapMotor::setStepOffsetInteractive() {
  Serial.println("-------------------------------------------");
  Serial.print("Current Step Offset: ");
  Serial.println(stepOffset);
  Serial.println("Change offset? (y/n): ");

  while (Serial.available() == 0);
  char response = Serial.read();
  while (Serial.available()) Serial.read();  // Clear buffer

  if (response == 'y' || response == 'Y') {
    Serial.println("Enter new offset (integer): ");
    while (Serial.available() == 0);
    stepOffset = Serial.readStringUntil('\n').toInt();
    config.setStepOffset(stepOffset);  // <-- Save persistently
    Serial.print("New Step Offset set to: ");
    Serial.println(stepOffset);
  } else {
    Serial.println("No changes made.");
  }
}


void SplitFlapMotor::moveSteps(int steps) {
  Serial.print("Moving forward ");
  Serial.print(steps);
  Serial.println(" steps...");
  motorBusy = true;
  stepper.moveTo(stepper.currentPosition() + steps);
  while (stepper.distanceToGo() != 0) stepper.run();
  Serial.println("Done.");
  motorBusy = false;
}

void SplitFlapMotor::goToCharacter(char inputChar) {
  inputChar = toupper(inputChar);
  int targetIndex = getCharacterIndex(inputChar);
  if (targetIndex == -1) {
    Serial.println("Character not in index.");
    return;
  }
  goToIndex(targetIndex);
}
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

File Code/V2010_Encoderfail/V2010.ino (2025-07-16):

/* This code works to index the drum based on the rotary encoder, and it is somewhat precise
but not very accurate. It keeps returning to the same flaps, but the flaps are not by each other
and it doesn't make much sense. Apparently we are only using half of the rotary encoder resolution,
so v2011 will move to full resolution instead of half.*/



#include <AccelStepper.h>

// --- Pin Definitions ---
#define IN1 5         // Stepper motor coil 1
#define IN2 4         // Stepper motor coil 2
#define IN3 2         // Stepper motor coil 3
#define IN4 15        // Stepper motor coil 4
#define ENCODER_A 14  // Rotary encoder signal A (Brown wire)
#define ENCODER_B 12  // Rotary encoder signal B (Blue/White wire)
#define HALL_PIN 34   // Hall effect sensor signal pin

// --- Constants ---
#define MOTOR_SPEED 200            // Motor speed in steps per second
#define OFFSET_COUNT 215           // Encoder count to move past the magnet before setting zero

// --- Globals ---
AccelStepper stepper(AccelStepper::FULL4WIRE, IN1, IN3, IN2, IN4);
volatile int encoderCount = 0;     // Tracks rotary encoder position
volatile bool directionCW = true;  // Tracks encoder rotation direction

// Interrupt handler for rotary encoder
void IRAM_ATTR handleEncoder() {
  bool A = digitalRead(ENCODER_A);
  bool B = digitalRead(ENCODER_B);
  if (A == B) {
    encoderCount++;
    directionCW = true;
  } else {
    encoderCount--;
    directionCW = false;
  }
}

// Zero the encoder when the magnet is detected, then move to a defined offset
void zeroEncoderAndOffset() {
  Serial.println("Searching for magnet to zero position using encoder...");

  // If magnet is already detected at startup, move forward to clear it
  if (digitalRead(HALL_PIN) == LOW) {
    Serial.println("Magnet detected at startup — moving past it to begin search...");
    stepper.moveTo(512);  // Move forward ~1/8 turn
    while (stepper.distanceToGo() > 0) {
      stepper.run();
    }
  }

  // Set motor to run at a steady speed
  stepper.setSpeed(MOTOR_SPEED);
  bool magnetDetected = false;

  // Continue rotating until hall sensor detects magnet
  while (!magnetDetected) {
    stepper.runSpeed();
    if (digitalRead(HALL_PIN) == LOW) {
      magnetDetected = true;
      Serial.print("Magnet detected at encoder count: ");
      Serial.println(encoderCount);
      break;
    }
  }

  // Move further by offset value using encoder readings
  long startEncoder = encoderCount;
  long targetEncoder = startEncoder + OFFSET_COUNT;
  Serial.print("Moving to offset target count: ");
  Serial.println(targetEncoder);

  while (encoderCount < targetEncoder) {
    stepper.runSpeed();
  }

  // Zero encoder and stepper
  encoderCount = 0;
  stepper.setCurrentPosition(0);
  Serial.println("Offset applied and encoder zeroed.");
  delay(500);
}

void setup() {
  Serial.begin(115200);
  delay(500);
  Serial.println("\n--------------------------------------------");
  Serial.println("Starting stepper + encoder + hall tracking...");

  // Set up encoder pins with pull-ups and attach interrupt
  pinMode(ENCODER_A, INPUT_PULLUP);
  pinMode(ENCODER_B, INPUT_PULLUP);
  attachInterrupt(digitalPinToInterrupt(ENCODER_A), handleEncoder, CHANGE);

  // Set up Hall effect sensor pin
  pinMode(HALL_PIN, INPUT);

  // Configure stepper motor
  stepper.setMaxSpeed(MOTOR_SPEED);
  stepper.setSpeed(MOTOR_SPEED);
  stepper.setAcceleration(800);

  // Perform initial zeroing
  zeroEncoderAndOffset();
}

void loop() {
  // Loop left empty for now to isolate and troubleshoot zeroing
}

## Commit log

2025-07-16 Added Current 3d files
    [Back_Bracket_1.stl, Bottom005.stl, BreakoutBoard.skp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]
2025-07-16 First upload
    Upload of initial files for final project. Includes several "Archive" folders, so sorry for that.
    [250mm_bed_1.3mf, 250mm_bed_1_a.stl, 250mm_bed_1_b.stl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]
